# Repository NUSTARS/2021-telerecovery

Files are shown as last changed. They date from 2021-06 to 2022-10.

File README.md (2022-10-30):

# Recovery Systems Telemetry Module (SkyNet)
A Telemetry Software-Hardware Package for High Powered Rockets.

# TODO:
- [ ] Implement storing data in onboard flash memory in transmitter board
- [ ] Implement GPS reading
- [ ] Use sensor readings to determine apogee
- [ ] Move calculations to groundstation when feasilble such as altitude from pressure
- [ ] Calculate pressure with current temperature from sensor for greater accuracy
- [ ] Improvements on groundstation

## Useage

The easiest way to use the code in this repo is to download PlatformIO and use the provided platformio.ini initialization file when you create a new project. PlatformIO works great with VS code. 

Checkout the [Wiki](https://github.com/NUSTARS/2021-telerecovery/wiki/Hardware) page for more information. 

### Google Drive
Here is a [Google Drive link](https://drive.google.com/drive/u/1/folders/1rWdLhBEQf0NXYTq_rxv_L2-M3DT5xfJa) for anything else we may not want to put on GitHub like pictures, videos, test results, etc.

## Initial Objectives:
- Under $200 total 
- 2 mile range to be safe
  - Assuming typical NSL flight profile, apogee is typically between 4000-6000ft 
- Small form factor
  - Do not want to take up too much space in the rocket 
- Detect separation of launch vehicle
- Collect as much data as possible; acceleration, gyro, pressure, temperature
- Protected from black powder residue
- Remember to consider the fact that carbon fiber is RF opaque
- Cross-platform desktop GUI application for displaying sensor data in a nice way

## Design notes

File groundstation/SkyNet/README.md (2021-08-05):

# SkyNet
SkyNet is a ground station software for High Powered Rockets.

## Features
TBD

## Useful Commands

In the project directory, you can run:

#### `npm install`

Install all the dependencies using npm, assuming you already have Node.js and Python installed in your environment.

#### `npm start`

Runs the app in the development mode.

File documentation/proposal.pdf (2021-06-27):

# Recovery System Telemetry Module

### Nicholas Marks

### June 2021

## Contents

1 Overview | 3
2 Project Outline | 3

## 1 Overview

A crucial part of engineering is recovering from mistakes and critically analyzing failures. However, it often is not as easy as one might think to determine exactly what went wrong after a system has failed. The NSL team from this past year is very familiar with this scenario. After the first test flight when the drogue parachute failed to deploy, nobody was 100% certain what the cause was. For peace of mind during the nail-biting few minutes of the launch as well as to aid in postlaunch analysis, I am proposing the development of a recovery system status detection module. The goal of this project would be to make a compact electromechanical system capable of detecting whether or not parachutes have deployed from the launch vehicle and sending this information to a ground station receiver. Furthermore, the system would also transmit the status of black powder ejection charges throughout the flight. Time permitting, other useful features could be added to the system as they are thought of.
Although a system such as this one is not entirely necessary (since after receiving information of a recovery system failure it would already be too late to remedy the problem), it can be a excellent learning experience for everyone involved. This also can greatly aid in safety since those on the ground can prepare themselves for a ballistic descent if the ground team knows in advance that such a descent is likely.

## 2 Project Outline

This project will involve both electrical and mechanical systems, so people of any background are encouraged to participate. The project can be broken up into the following sections listed below. This list is non-exhaustive and more will be thought of as the project is underway.

1. Electronics design
- Which microcontroller will we use?
- What peripherals will we need? (Sensors, transmitters, etc.)
- How will the board be layed out and will be use a PCB?
- Design of the ground station
2. Mechanical design
- How will the electronics be housed to minimize space and weight?
- How will the electronics/housing be securing in a rocket?
3. Software/hardware interface and detection systems
- How will the system detect separation of the launch vehicle?
- How will the system detect ejection charge status?

### 2.1 Timeline

A rough timeline is presented in Table 1. This is a very rough estimate and it is likely it will change greatly as the project is underway and the various parts of the project are better understood.

7/1 to 7/15 | Initial design phase
7/15 to 8/5 | Prototyping electrical components
8/5 to 8/15 | Prototyping mechanical components
8/15 to end | Final testing/modifications

Table 1: Rough Project Timeline

### 2.2 Learning Objectives

Considering many NUSTARS members may not have all the required experience to undertake this project immediately, emphasis will be placed on learning new skills along the way. Some topics we will get the chance to learn about through this project are:

- Microcontroller programming and interfacing with external modules/peripherals
- Git source control and GitHub
- RF data transmission
- CAD
- Basic 3D printing/manufacturing

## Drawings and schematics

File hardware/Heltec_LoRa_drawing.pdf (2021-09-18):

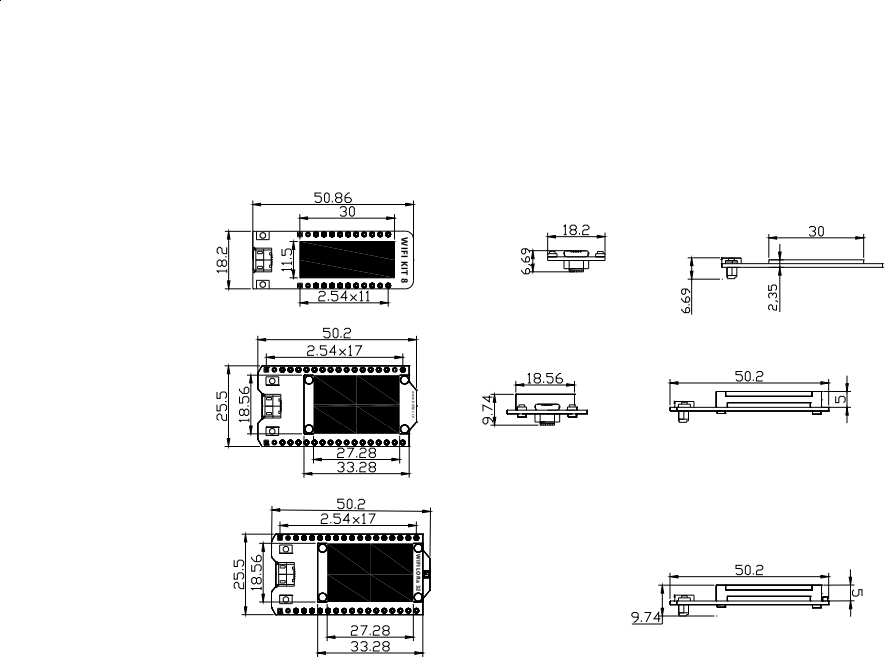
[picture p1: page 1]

W 8 TI KI FI nc. c etl eh. ww w 23 aR OLI FI W

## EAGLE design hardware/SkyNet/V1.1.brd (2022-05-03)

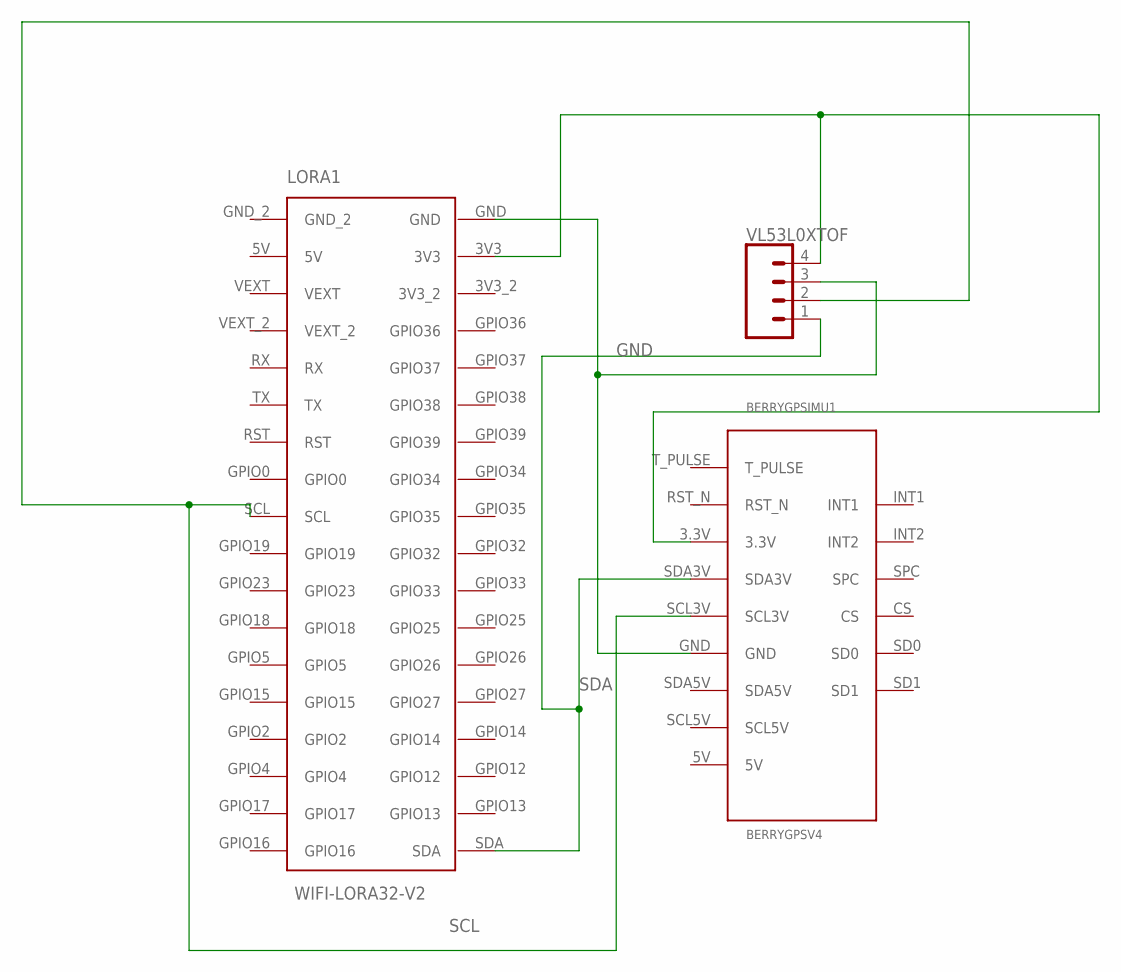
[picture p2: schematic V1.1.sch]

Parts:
BERRYGPSIMU1: BERRYGPSV4
LORA1: WIFI-LORA32-V2
VL53L0XTOF: CONN_04JST-PTH-VERT; JST-4-PTH-VERT

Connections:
5V: BERRYGPSIMU1.3.3V, LORA1.3V3, VL53L0XTOF.4
GND: BERRYGPSIMU1.GND, LORA1.GND, VL53L0XTOF.3
SCL: BERRYGPSIMU1.SCL3V, LORA1.SCL, VL53L0XTOF.2
SDA: BERRYGPSIMU1.SDA3V, LORA1.SDA, VL53L0XTOF.1

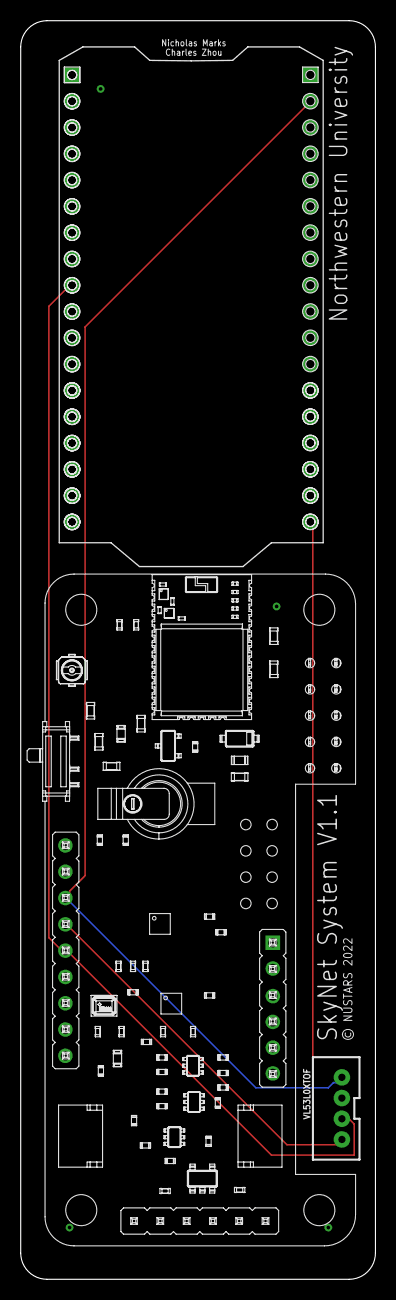
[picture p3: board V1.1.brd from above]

Board: 2 copper layers, 34.3 x 121.6 mm, 3 parts (0 on the bottom side), 4 nets.

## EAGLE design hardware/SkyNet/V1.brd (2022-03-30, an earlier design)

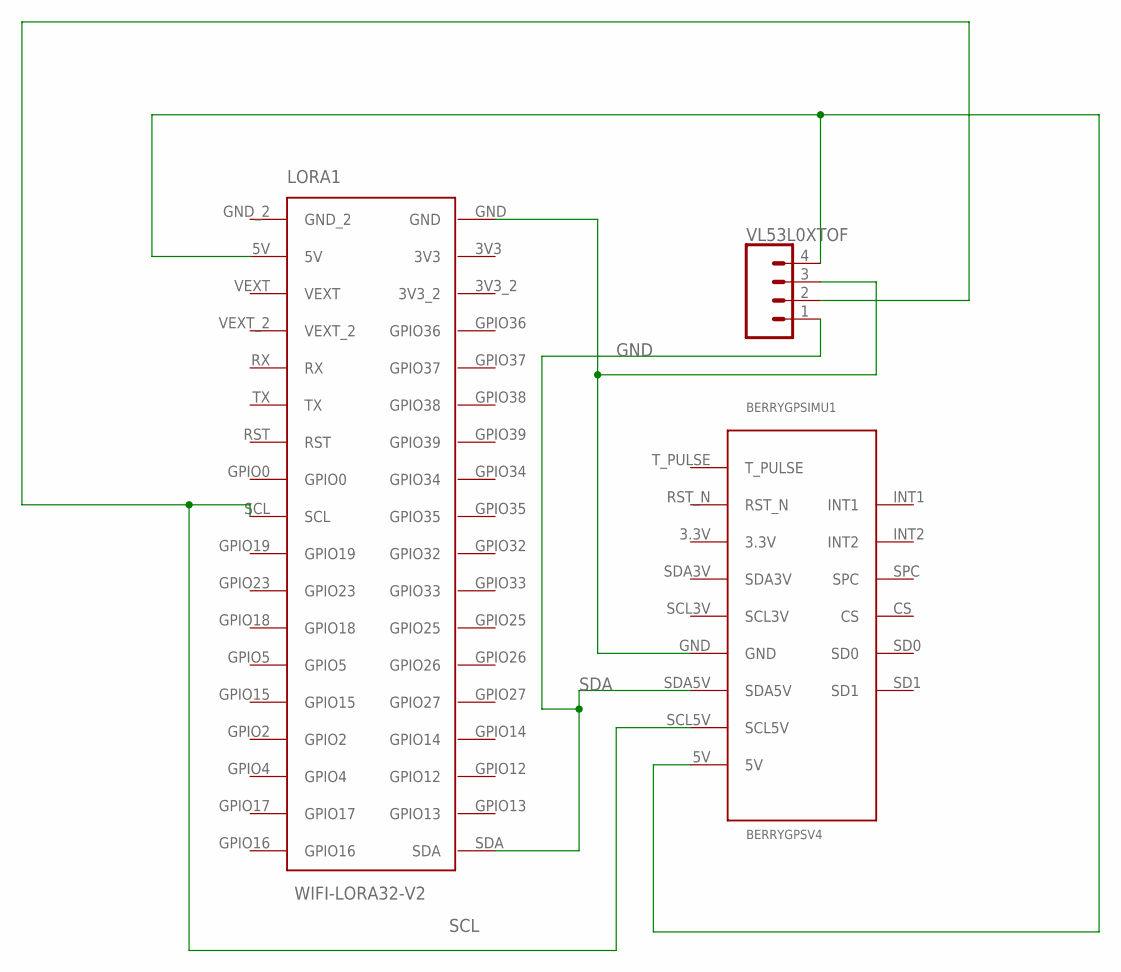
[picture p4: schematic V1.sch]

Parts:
BERRYGPSIMU1: BERRYGPSV4
LORA1: WIFI-LORA32-V2
VL53L0XTOF: CONN_04JST-PTH-VERT; JST-4-PTH-VERT

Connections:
5V: BERRYGPSIMU1.5V, LORA1.5V, VL53L0XTOF.4
GND: BERRYGPSIMU1.GND, LORA1.GND, VL53L0XTOF.3
SCL: BERRYGPSIMU1.SCL5V, LORA1.SCL, VL53L0XTOF.2
SDA: BERRYGPSIMU1.SDA5V, LORA1.SDA, VL53L0XTOF.1

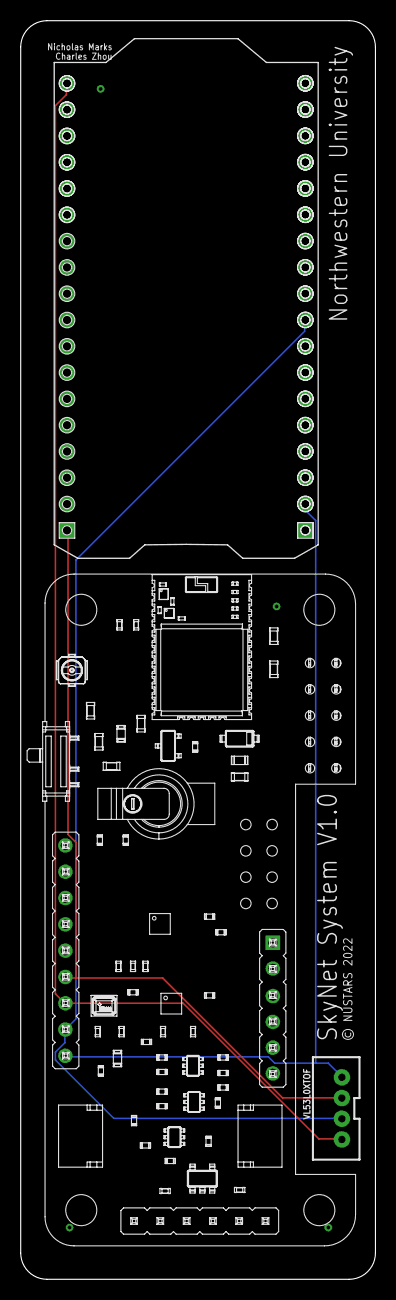
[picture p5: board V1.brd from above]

Board: 2 copper layers, 34.3 x 121.6 mm, 3 parts (0 on the bottom side), 4 nets.

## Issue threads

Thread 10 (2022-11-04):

Battery power and wiring

chazzhou, 2022-11-04:
As of now, the battery power doesn't work. Vext is not functional. Need to figure out Vext 3.3V control and update the PCB wiring.

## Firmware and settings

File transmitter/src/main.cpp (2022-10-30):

#include "transmitter.h"  

// Declare sensor objects
Adafruit_VL53L0X ToF = Adafruit_VL53L0X(); // time of flight
Adafruit_BMP3XX bmp; // pressure                  

// variables to store IMU data
Adafruit_Sensor *accelerometer, *gyroscope, *magnetometer; // IMU
// see the the LSM6DS_LIS3MDL file in this project to change board to LSM6DS33, LSM6DS3U, LSM6DSOX, etc
#include "LSM6DS_LIS3MDL.h"
sensors_event_t mag_event, gyro_event, accel_event;

unsigned long startTime; // time for loop
int loopcount = 0;

/*--------------------------------------------------*/
void setup(void) {

  // Start Heltec LoRa ESP32 Board
  Heltec.begin(
      false /*DisplayEnable Enable*/,
      true /*LoRa enable*/,
      true /*Serial Enable*/,
      true /*PABOOST Enable*/,
      BAND /*long BAND*/);
  delay(500); // wait for board to be initialized

  Serial.begin(115200); // init serial for testings
  while (!Serial) delay(10);  

  pinMode(21, OUTPUT);
  digitalWrite(21, LOW); // Enable Vext

  // Initialize time of flight sensor
  if (!ToF.begin()) {
    Serial.println(F("Failed to boot VL53L0X"));
    while(1) {;}
  } else {
    Serial.println(F("Booted VL53L0X"));
  }

  // Initialize BMP388 pressure sensor
  if (!bmp.begin_I2C()) {
    Serial.println(F("Failed to boot BMP388"));
    while (1);
  } else {
    Serial.println(F("Booted BPM388"));
  }

  // Set up oversampling and filter initialization on the BMP388
  bmp.setTemperatureOversampling(BMP3_OVERSAMPLING_8X);
  bmp.setPressureOversampling(BMP3_OVERSAMPLING_4X);
  bmp.setIIRFilterCoeff(BMP3_IIR_FILTER_COEFF_3);
  bmp.setOutputDataRate(BMP3_ODR_50_HZ);

  // Uncomment Serial.print statements for debugging 

  // Initialize IMU sensors
  if (!init_sensors()) {
    Serial.println(F("Failed to find IMU sensors"));
    while (1) delay(10);
  } else {
    Serial.println(F("Booted IMU sensors"));
  }

  // Print out sensor information
  accelerometer->printSensorDetails();
  gyroscope->printSensorDetails();
  magnetometer->printSensorDetails();

  setup_sensors();
  
  Wire.setClock(400000); // 400KHz
}

void loop() {

  startTime = millis();

  // Read pressure sensor (float)
  if (!bmp.performReading()) {
    return;
  }

  // Read time of flight sensor (unsigned short)
  VL53L0X_RangingMeasurementData_t val = read_ToF(ToF);
  uint16_t tof_data=0;
  if (val.RangeStatus != 4) {
    tof_data = val.RangeMilliMeter;
  } else {
    // if data is bad (probably nothing in range) set equal to zero
    tof_data = 0;
  }

  // Read IMU data (all floats)
  magnetometer->getEvent(&mag_event);
  gyroscope->getEvent(&gyro_event);
  accelerometer->getEvent(&accel_event);
  
  // Pack up the data into an array
  char buffer[150];
  char data_format[] = "%hu,%f,%f,%f,%f,%f,%f,%f,%f,%f,%f,%f,%f";

  sprintf(buffer,data_format,
    tof_data,
    bmp.temperature,
    bmp.pressure,
    bmp.readAltitude(SEALEVELPRESSURE_HPA),
    accel_event.acceleration.x,
    accel_event.acceleration.y,
    accel_event.acceleration.z,
    gyro_event.gyro.x,
    gyro_event.gyro.y,
    gyro_event.gyro.z,
    mag_event.magnetic.x,
    mag_event.magnetic.y,
    mag_event.magnetic.z
  );

  float temptemperature = bmp.temperature;
  float temppressure = bmp.pressure;
  float tempaltitude = bmp.readAltitude(SEALEVELPRESSURE_HPA);
  
  LoRa.beginPacket();
  LoRa.setSignalBandwidth(500E3);
  LoRa.setTxPower(20,RF_PACONFIG_PASELECT_PABOOST);
  LoRa.write((uint8_t)tof_data);
  LoRa.write((uint8_t *) &temptemperature, 4);
  LoRa.write((uint8_t *) &temppressure, 4);
  LoRa.write((uint8_t *) &tempaltitude, 4);
  LoRa.write((uint8_t *) &accel_event.acceleration.x, 4);
  LoRa.write((uint8_t *) &accel_event.acceleration.y, 4);
  LoRa.write((uint8_t *) &accel_event.acceleration.z, 4);
  LoRa.write((uint8_t *) &gyro_event.gyro.x, 4);
  LoRa.write((uint8_t *) &gyro_event.gyro.y, 4);
  LoRa.write((uint8_t *) &gyro_event.gyro.z, 4);
  LoRa.write((uint8_t *) &mag_event.magnetic.x, 4);
  LoRa.write((uint8_t *) &mag_event.magnetic.y, 4);
  LoRa.write((uint8_t *) &mag_event.magnetic.z, 4);
  LoRa.endPacket();

  // Each loop should be at least 20ms.
  while(millis() - startTime < (DT*1000)) {
    // wait
  }
 
} // END LOOP

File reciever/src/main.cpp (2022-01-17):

/*
  Adapted from .pio\libdeps\heltec_wifi_lora_32_V2\\examples\LoRa\OLED_LoRa_Reciever.ino
*/

// #include "reciever.h"
#include <Arduino.h>
#include "OLED.h"
#include "LoRa_RX.h"
#define DT  0.02

String rssi = "RSSI --";
String packSize = "--";
String packet;

void setup() { 
  Serial.begin(115200);
  
  Heltec.begin(
    true /*Display Enabled*/,
    true /*Heltec.Heltec.Heltec.LoRa Disable*/, 
    true /*Serial Enable*/, 
    true /*PABOOST Enable*/, 
    BAND /*long BAND*/);

  OLED_init(); // Initialize the OLED screen
 
  LoRa.setSignalBandwidth(500E3); // must match transmitter
 
  LoRa.receive(); // Initialize LoRa for recieving
}

int count = 0;
unsigned long startTime;

void loop() {

  startTime = millis();

  char msg[50];

  int packetSize = LoRa.parsePacket();
  
  if (packetSize){
    OLED_clear();

    cbk(packetSize); // recieve and print recieved packet

    count ++;
    sprintf(msg,"Packet received: %d",count);
    OLED_print(0,26,MAX_SCREEN_WIDTH,msg);
  }

  // Each loop should be at least 20ms.
  while(millis() - startTime < (DT*1000)) {
    // wait
  }
  
}

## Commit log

2021-07-19 create ground_station platformio project, add example code
2021-07-21 ToF sensor test works
2021-07-29 Added SkyNet groundstation software
    Initial version
2021-07-29 add serial printing, other updates
2021-07-29 add serial printing
2021-09-06 add BerryIMU sample code to test dir
2021-09-16 all sensors working
2021-09-16 package data into array first, then print, and other updates
2021-09-16 updates to printing
2021-09-17 added gyro and CF angles to data, transmission is also faster now
2021-09-18 add eagle files
    [gerber_job.gbrjob, schem.GBL, schem.GBO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]
2021-09-18 fix eagle files
    [schem.brd]
2021-10-12 Bump electron from 13.1.8 to 13.3.0 in /groundstation/SkyNet
    Bumps [electron](https://github.com/electron/electron) from 13.1.8 to 13.3.0.
    - [Release notes](https://github.com/electron/electron/releases)
    - [Changelog](https://github.com/electron/electron/blob/main/docs/breaking-changes.md)
    - [Commits](https://github.com/electron/electron/compare/v13.1.8...v13.3.0)
    ---
    updated-dependencies:
    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
2021-12-18 add comments, increase buffer size to prevent overflow
    [main.cpp, transmitter.h]
2021-12-21 move Adafruit_AHRS
    [bunny.obj]
2021-12-25 compiles but doesn't find sensor
    [main.cpp]
2021-12-25 IMU data output looks good!
2021-12-25 IMU is working I think
2021-12-25 moved stuff to test
    [bunny.obj]
2021-12-26 9(IMU)+4(ToF and BMP) dof sensors all output good data
2021-12-28 removed calibration stuff and added lora transmission
2021-12-29 overhall sensor reading with new adafruit libraries
2021-12-29 Removed IMU.c and IMU.cpp because they are no longer needed (I think)
    [main.cpp, transmitter.h]
2021-12-29 forgot to remove a print
2021-12-29 change 20ms delay, arduino delay() function is bad
2022-01-08 Revert "Merge branch 'main' of https://github.com/NUSTARS/2021-telerecovery"
    This reverts commit 339799553d41e9301c50609017da7b716ce3b563, reversing
    changes made to cd481ba09471f784a15fa7aeb49dcb35e36d6197.
    [easy_serial.py, main.cpp, read_serial.py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]
2022-01-08 Revert "Update Skynet"
    This reverts commit cd481ba09471f784a15fa7aeb49dcb35e36d6197.
    [main.cpp, renderer.js]
2022-01-08 Revert "Revert "Merge branch 'main' of https://github.com/NUSTARS/2021-telerecovery""
    This reverts commit 8990767382afad5a45817f910757894a7d4a18d8.
    [easy_serial.py, main.cpp, read_serial.py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]
2022-01-08 Bug fixes
    Fixed the chart starting position issue (zero)
    Fixed the serial devices update frequency (low)
    [renderer.js]
2022-03-23 Bump minimist from 1.2.5 to 1.2.6 in /groundstation/SkyNet
    Bumps [minimist](https://github.com/substack/minimist) from 1.2.5 to 1.2.6.
    - [Release notes](https://github.com/substack/minimist/releases)
    - [Commits](https://github.com/substack/minimist/compare/1.2.5...1.2.6)
    - dependency-name: minimist
    dependency-type: indirect
    ...
    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
2022-04-07 Bump plist from 3.0.4 to 3.0.5 in /groundstation/SkyNet
    Bumps [plist](https://github.com/TooTallNate/node-plist) from 3.0.4 to 3.0.5.
    - [Release notes](https://github.com/TooTallNate/node-plist/releases)
    - [Changelog](https://github.com/TooTallNate/plist.js/blob/master/History.md)
    - [Commits](https://github.com/TooTallNate/node-plist/commits)
    - dependency-name: plist
    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
2022-04-07 Bump electron from 13.6.3 to 13.6.6 in /groundstation/SkyNet
    Bumps [electron](https://github.com/electron/electron) from 13.6.3 to 13.6.6.
    - [Commits](https://github.com/electron/electron/compare/v13.6.3...v13.6.6)
    - dependency-name: electron
    dependency-type: direct:development
    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
2022-04-07 Bump simple-get from 4.0.0 to 4.0.1 in /groundstation/SkyNet
    Bumps [simple-get](https://github.com/feross/simple-get) from 4.0.0 to 4.0.1.
    - [Release notes](https://github.com/feross/simple-get/releases)
    - [Commits](https://github.com/feross/simple-get/compare/v4.0.0...v4.0.1)
    - dependency-name: simple-get
    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
2022-05-03 Update Board Pinout PDF
2022-05-03 Correct PCB for internal LiPO
    5V bus -> 3V3
    [V1.1.brd, V1.1.sch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]
2022-05-03 Create WIFI_LoRa_32_V2.1(868-915) Schematic.PDF
2022-10-30 Fixed BMP3XX library and bump dependencies
    [main.cpp]

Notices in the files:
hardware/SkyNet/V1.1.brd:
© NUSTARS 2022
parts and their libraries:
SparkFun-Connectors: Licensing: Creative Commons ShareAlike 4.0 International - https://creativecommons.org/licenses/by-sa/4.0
